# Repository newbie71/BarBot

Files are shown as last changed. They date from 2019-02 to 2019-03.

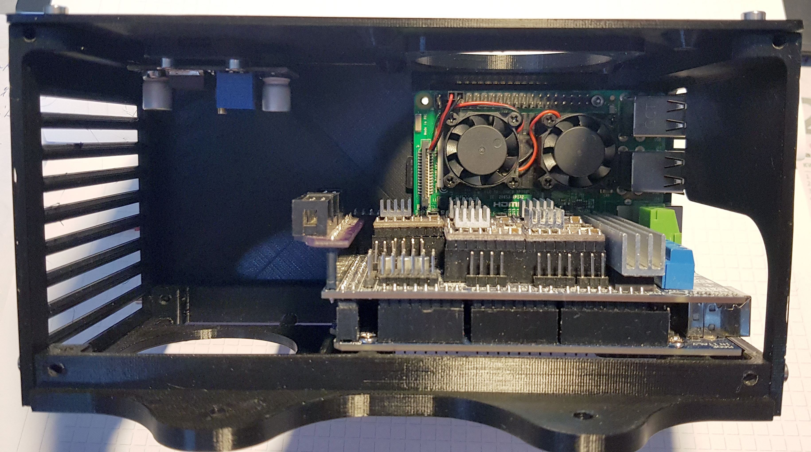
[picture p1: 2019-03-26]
Pics/20190226_145837a.jpg

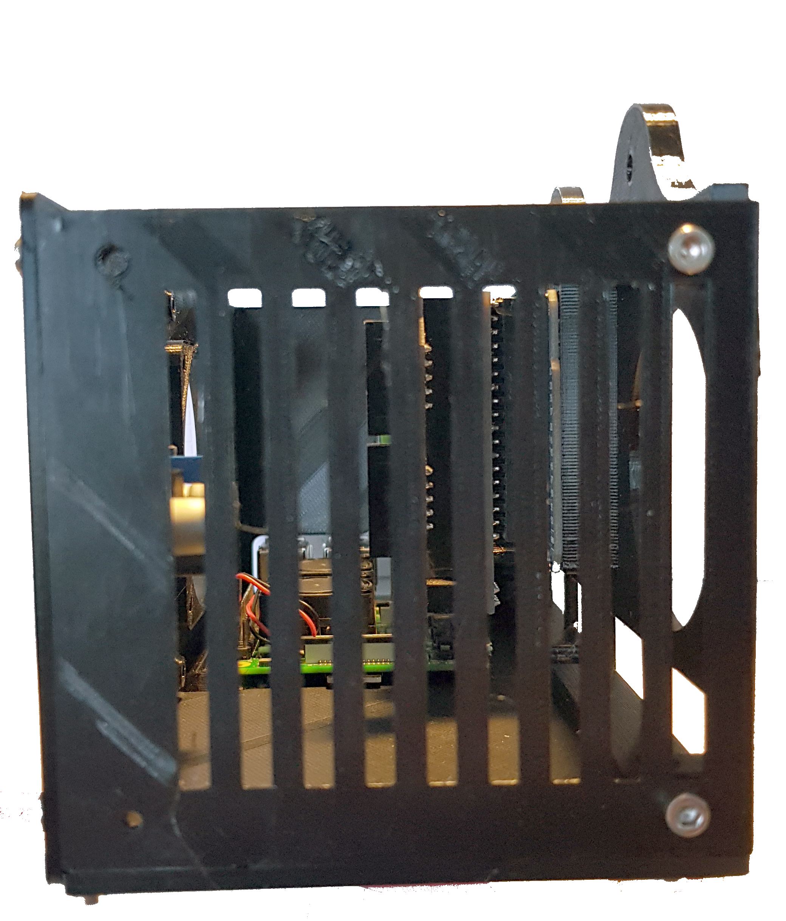
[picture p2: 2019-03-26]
Pics/20190226_150021a.jpg

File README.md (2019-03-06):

# BarBot fork from sexycyborg
An Automated Bartender powered by Arduino  

Based on the work of Lukas Šidlauskas:  
https://create.arduino.cc/projecthub/sidlauskas/barbot-cocktail-mixing-robot-0318aa  
https://github.com/sidlauskaslukas/barbot

Based on the work of Naomi Wu

https://github.com/sexycyborg/BarBot/

## About

For my BarBot I wanted to make sure it was rock-solid reliable.
16 popular drinks (15 alcoholic and 1 non-alcoholic for non-drinkers and so that children can participate with supervision) are available from 16 arcade style buttons. A printed menu lists what button number corresponds to which drink.

Since the BarBot is designed for a working bars, party or company environments, it had to do without pumps or difficult to clean feed lines. All of the components that require nightly cleaning are the same that bar staff are already accustomed to cleaning- spirit measures and bar mats. All drive components and bearings have been moved from under the pour spouts to well above or behind so there is no risk of an accumulation of sugar-rich liquids gumming up hard to clean moving parts of the machine or attracting vermin.

This BarBot is a functional novelty- it's something fun for visitors to play with. Perfect for my home and company where a large number of patrons are tech professionals. It is not secured for true commercial use- and with a bar full of half-drunk hardware engineers it would be pointless to try. In this case, it's better to rely on good faith then pretend you could stop them if challenged. Patrons could still manually press their cups to the spirit measures to manually dispense alcohol if they wanted to- but they could also reach over the bar and steal liquor while the bartender's back was turned. So far none have because why ruin the fun when there's no "hack" in doing so? If you really wanted to, a clear acrylic panel could be added to the front to prevent any manual dispensing, but it's really a lot less fun that way.

Portion control and payment is handled via an inexpensive arcade token acceptor. A customer can pay the bartender for a cup of ice and a token. When the correct token is inserted into the BarBot a contact is momentarily closed. The customer then has 60 seconds to press a drink selection button. That same contact can be closed with the key switch, in which case no tokens are needed for any orders while the switch is in that position.

Barbots of this configuration typically use either a servo or a stepper motor with a lead screw to depress the spirit measure spout depending on the type of dispenser it is. My code changes allow for either as RAMPS boards can control both steppers and a servo.

In the build and demonstration videos, you'll see that the full 25ml "shot" the spirit measure contains is usually only partially dispensed. This is because the actual shot size is defined in the code as a function of how long the spout is depressed. This allows for finer tuning of the drink flavor and portion size which would not be possible if only 25ml increments were used.

This BarBot was designed to be easy to build with off-the-shelf OpenBuilds components, V-Slot aluminum extrusion, and low-cost 3D printer parts. The heart of the BarBot is a standard Arduino Mega, RAMPS 1.6 and TMC2xxx or DRV8825 stepper driver combination as used in many 3D printers. But my prefered combination is a BIQU re-arm clone,RAMPS 1.6+ and TMC2130 V1.1 spi.

BarBot<BR>
See [Build Guide](https://github.com/sexycyborg/BarBot/blob/master/BarBotDrwMk01.PDF). 
  *Guide and SolidWorks CAD drawings courtesy of [Vexelius](https://www.thingiverse.com/Vexelius/).*

## Attention this BOM variats from the Sexyborg due to high cost's and shipment from openbuilds-store  
### All sources including prices can be found in the BOM Excel-sheet

## BOM

The BOM can be found here https://github.com/newbie71/BarBot/blob/master/BOM_Barbot_1.0.xlsx 
with links where to order and the cost.

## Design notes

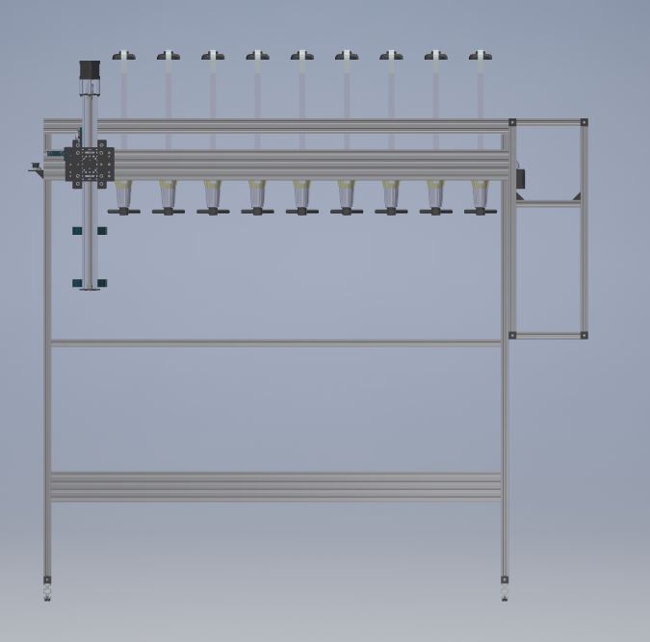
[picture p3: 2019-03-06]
Pics/Barbot_04.JPG

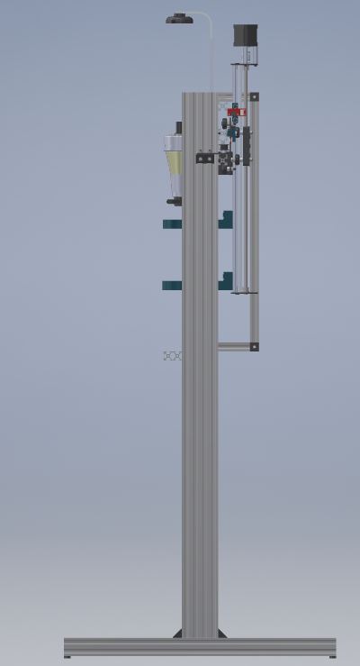
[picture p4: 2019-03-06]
Pics/Barbot_02.JPG

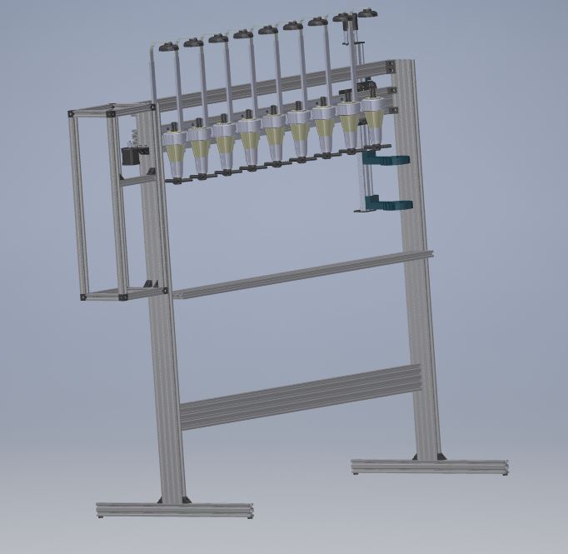
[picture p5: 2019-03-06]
Pics/Barbot_05.JPG

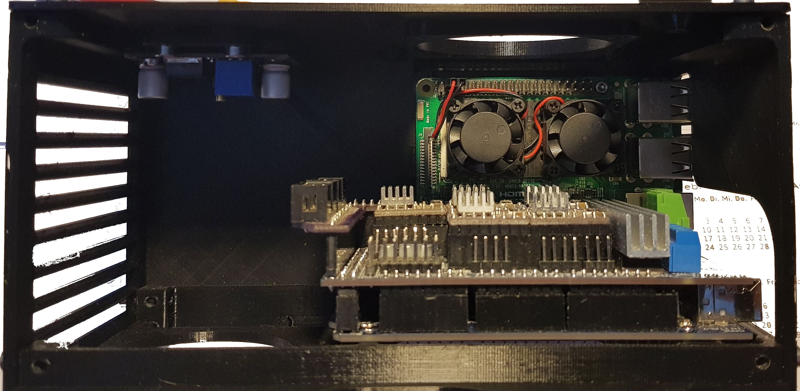
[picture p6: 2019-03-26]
Pics/20190226_145816_a.jpg

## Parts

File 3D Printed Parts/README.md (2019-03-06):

# Naomi Wu's BarBot
An Automated Bartender powered by Arduino  

All parts can be printed in PETG at 0.2mm layer height, 30% infill.

## Additional 3D Files Required:

[Quick Release RAMPS Holder for T-Slot Profile](https://www.thingiverse.com/thing:2169986)  

[2020 Cable Zip Tie Mount for M5x10 screws (optional fins)](https://www.thingiverse.com/thing:2486032)

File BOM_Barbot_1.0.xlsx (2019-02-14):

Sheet: newbie71
QTY | Description | Source
 |  |  | SP | TP
Frame |  |  | EP2 | GP2
1.00 | Ramps Kit 1.4 | Ramps 1.4 kit (https://www.aliexpress.com/item/3D-Printer-1pc-Mega-2560-R3-1pc-RAMPS-1-4-control-panel-5pcs-DRV8825-Stepper-Motor/32599773680.html) | 16.66 | 16.66 | €
1.00 | Ramps SD Card Reader | SD Card-Ramps (https://www.aliexpress.com/item/New-TF-SD-Card-SD-Ramps-3D-Printer-Assembling-Module-For-Ramps-1-4-Diy-Kit/32958286211.html) | 1.09 | 1.09 | €
2.00 | 10x10 Drag chain 2 Meters | Drag-Chain-L1000mm (https://www.aliexpress.com/item/Drag-Chain-L1000mm-Transmission-Chains-10-x-10mm-Cable-Wire-Carrier-with-end-connectors-for-CNC/32852286371.html) | 4.16 | 8.32 | €
1.00 | V-Slot 1200mm (horizontal carriage rail) | v-slot linear Rail 1200mm (https://jamoprint.com/CNC-Profile-Linearprofile---Zubehoer/Alu-Profile/CNC-Linearprofil-V-Slot-20x20x1000-28-29-30-48.html) | 30.90 | 30.90 | €
2.00 | Alu-Profile 2080 1200mm (Two vertical risers ) | Alu-Profile 2080 (https://www.ebay.de/i/323427289717?chn=ps&var=512489777539) | 25.00 | 50.00 | €
2.00 | Alu-Profile 2080 1160mm (Lower brace, shelf for bar mat) | Alu-Profile 2080 (https://www.ebay.de/i/323427289717?chn=ps&var=512489777539) | 25.00 | 50.00 | €
1.00 | Alu-Profile 2040, 1200mm (Horizontal rail for drag chain) | Alu-Profile 2040 (https://www.ebay.de/itm/Systemprofil-20x40-2040-Nut-6-Strebenprofil-Aluprofil-Konstruktionsprofil/323655543211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) | 17.10 | 17.10 | €
2.00 | Alu-Profile 2040 600mm (Horizontal legs) | Alu-Profile 2040 (https://www.ebay.de/itm/Systemprofil-20x40-2040-Nut-6-Strebenprofil-Aluprofil-Konstruktionsprofil/323655543211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) | 8.70 | 17.40 | €
1.00 | V-Slot® NEMA 17 Linear Actuator Bundle 500mm | V-Slot sliding table 500mm (https://www.aliexpress.com/item/Effective-travel-400mm-linear-Sliding-table-total-length-494mm-T8-Screw-2060-V-slot-with-42/32917601483.html) | 47.82 | 47.82 | €
1.00 | V-Slot Gantry Set , 20mm - 80mm (Universal) | V-Slot-Gantry-Set (https://www.aliexpress.com/item/Funssor-Assembled-Black-Color-V-Slot-Gantry-Set-For-DIY-Openbuilds-CNC-milling/32957873797.html) | 14.39 | 14.39 | €
1.00 | Motor Mount Plate Nema17 | V-Slot-NEMA-17-Linear-Actuator-Bundle-Kit (https://www.aliexpress.com/item/V-Slot-NEMA-17-Linear-Actuator-Bundle-Diy-Belt-Driven-Kit-with-Nema-17-Stepper-Motor/32899784879.html) | 35.61 | 35.61 | €
2.00 | GT2-2m Timing Belt (per Meter) | GT2-2M 6MM (https://www.aliexpress.com/item/2M-3D-Printer-Accessories-2GT-6MM-10MM-PU-with-steel-core-GT2-Open-Timing-Belt-Width/32857079977.html) | 2.06 | 4.12 | €
2.00 | Black Angle Corner Connector | 25pcs-Cast-Corner-Bracket-for-V-Slot-T-slot (https://www.aliexpress.com/item/25pcs-lot-CNC-Aluminum-90-Degree-Cast-Corner-Bracket-for-V-Slot-T-slot-Linear-Rail/32870718238.html) | 9.99 | 19.98 | €
3.00 | M5*8 Low Profile Screws (10 pcs/pack) | 20pcs-M5-Low-Profile-Screws-M5 (https://www.aliexpress.com/item/3D-printer-parts-20pcs-M5-Low-Profile-Screws-M5-6-8-10-12-15-20-25mm/32963232719.html) | 0.97 | 2.91 | €
1.00 | M5*40 Low Profile Screws (10 pcs/pack) | Zylinderschrauben-DIN-7984-Edelstahl-V2A-M5-niedrig (https://www.ebay.de/itm/Zylinderschrauben-DIN-7984-Edelstahl-V2A-M5-niedrig-Innensechskant/281264548516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) | 2.30 | 2.30 | €
1.00 | M5*25 Low Profile Screws (10 pcs/pack) | 20pcs-M5-Low-Profile-Screws-M5x25mm (https://www.aliexpress.com/item/3D-printer-parts-20pcs-M5-Low-Profile-Screws-M5-6-8-10-12-15-20-25mm/32963232719.html) | 2.02 | 2.02 | €
1.00 | 3mm Aluminium Spacer | 3mm Aluminium Spacer (https://www.ebay.de/itm/Distanz-H%C3%BClse-M5-Abstandshalter-Distanzh%C3%BClse-Huelse-H%C3%BClse-Aluminium-dely-trade/121237081001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) | 2.41 | 2.41 | €
1.00 | 6mm Aluminium Spacer | 6mm Aluminium Spacer (https://www.aliexpress.com/item/5pcs-Bicycle-Water-Bottle-Holder-Spacer-M5-Washer-Aluminum-Alloy-6mm-Bike-Parts/32911691819.html) | 0.81 | 0.81 | €
1.00 | Tee Nuts M5 (10 pcs/pack) | 50pcs V-Slot-M5-Tee-Nut (https://www.aliexpress.com/item/50pcs-Lot-Micromake-3D-Printer-Parts-Tee-nuts-for-building-machine-V-Slot-M5-Tee-Nut/32689972745.html) | 4.87 | 4.87 | €
1.00 | Drop in Tee Nuts M5 | M5-Nickel-Plated-Tee-Nut-Hammer-Head-Attach-Nut (https://www.aliexpress.com/item/M3-M4-M5-Nickel-Plated-Tee-Nut-Hammer-Head-Attach-Nut-for-Aluminum-Extrusion-Profile-2020/32964717506.html) | 4.95 | 4.95 | €
1.00 | Nylon Insert Hex Locknut M5 (10 pcs/pack) | 50pcs-DIN98 M5 (https://www.aliexpress.com/item/50Pcs-DIN985-M2-M2-5-M3-M4-M5-M6-or-M8-20pcs-304-Stainless-Steel-Nylon/32865488252.html) | 3.59 | 3.59 | €
2.00 | 1250mm Slot Cover /Panel Holder | 1m 20-30-40-50-series-6mm-8mm-10mm-flat-seal (https://www.aliexpress.com/item/1meter-20-30-40-50-series-6mm-8mm-10mm-flat-seal-for-2020-aluminum-profile-soft/32840481329.html) | 0.76 | 1.52 | €
2.00 | Bar Mat | Barkeeper-Service-Matte-Trockenschalen (https://www.amazon.de/COSOOS-Gummi-%C3%9Cberlaufmatte-versch%C3%BCttungsfreies-Kaffee-Barkeeper-Service-Matte-Trockenschalen-Matten/dp/B07L46CCF3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) | 8.99 | 17.98 | €
Control Box
4.00 | Alu-Profile 2020 530mm (All with 5mm threaded ends) | Alu-Profile 2020 Nut-5 (https://www.ebay.de/itm/Aluminiumprofil-20x20-Nut-5-Alu-Profil-5-Strebenprofil-item-2020-100mm-1200mm/112881130983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) | 5.50 | 22.00 | €
5.00 | Alu-Profile 2020 165mm (All with 5mm threaded ends) | Alu-Profile 2020 Nut-5 (https://www.ebay.de/itm/Aluminiumprofil-20x20-Nut-5-Alu-Profil-5-Strebenprofil-item-2020-100mm-1200mm/112881130983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) | 1.50 | 7.50 | €
4.00 | Alu-Profile 2020 130mm (All with 5mm threaded ends) | Alu-Profile 2020 Nut-5 (https://www.ebay.de/itm/Aluminiumprofil-20x20-Nut-5-Alu-Profil-5-Strebenprofil-item-2020-100mm-1200mm/112881130983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) | 2.00 | 8.00 | €
8.00 | Cube Corner | V-slot-three-corner-cube-corner (https://www.aliexpress.com/item/3D-printer-openbuilds-V-slot-three-corner-cube-corner-prism-connector-adjustable-wheel-bracket-1pcs/32790791649.html) | 1.00 | 8.00 | €
2.00 | M5*15 Low Profile Screws (10 pcs/pack) | 20pcs-M5-Low-Profile-Screws-M5 (https://www.aliexpress.com/item/3D-printer-parts-20pcs-M5-Low-Profile-Screws-M5-6-8-10-12-15-20-25mm/32963232719.html) | 1.45 | 2.90 | €
1.00 | Coin Acceptor (Or similar if you modify the lower lasercut panel to fit) | Multi-Coin-Acceptor-CPU-Programmable (https://www.aliexpress.com/item/Multi-Coin-Acceptor-CPU-Programmable-6-Type-Coin-Validator-Electronic-Selector-Mechanism-Arcade-Mech-for-Vending/32901295765.h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) | 10.99 | 10.99 | €
2.00 | 27x27 Illuminated Arcade Buttons (min lot 20 pcs) | 27x27mm-Small-square-LED-Light-Illuminated-push-button (https://www.aliexpress.com/item/27-27mm-Small-square-LED-Light-Illuminated-push-button-switch-for-casino-slot-machine-gambling-game/32860066542.html) | 12.78 | 25.56 | €
1.00 | 22mm Emergency Stop Push Button Switch 12V DC LED Illuminated (or similar) | LAY7-Y090 Emergency-stop-light-power-22mm-switches (https://www.aliexpress.com/item/Emergency-stop-light-power-22mm-switches-mushroom-head-on-off-pushbutton-led-switch-lay37-lay7-Y090/32962801033.html) | 3.62 | 3.62 | €
1.00 | 22mm Key Selector Switch | LAY37-AC-380V-10A-DPST-3-Position-Rotary-Selector-Key-Lock-Switch (https://www.aliexpress.com/item/LAY37-AC-380V-10A-DPST-3-Position-Rotary-Selector-Key-Lock-Switch-1-N-O-1/32864589832.html) | 1.58 | 1.58 | €
1.00 | Power Socket Switch IEC 320 C14 | Panel-Mount-Rocker-Switch-IEC320-C14-3-Pin-Plug (https://www.ebay.de/itm/Panel-Mount-Rocker-Switch-IEC320-C14-3-Pin-Plug-Power-Socket-AC250V-10A-ST/192790286152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) | 1.55 | 1.55 | €
1.00 | 12v Power Supply, 150w (Part No. MS-150-12 or similar) | DC-12V-LED Power Supply (https://www.ebay.de/itm/DC-12V-24V-2A-30A-LED-Netzteil-Trafo-Schaltnetzteil-Adapter-Treiber-Power-Supply/162296585279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) | 19.67 | 19.67 | €
1.00 | Ribbon cable to 18 pin connector 40CM long | 1m-Flat-IDC-Ribbon-Extension-Cable (https://www.aliexpress.com/item/1m-Flat-IDC-Ribbon-Extension-Cable-Rainbow-DuPont-Wire-10P-14P-16P-20P-26P-34P-40P/32964398452.html) | 1.07 | 1.07 | €
 |  |  |  | 469.19 | €

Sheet: Sexycyborg BOM
QTY | Description | Source
 |  |  | SP | TP
1.00 | Ramps Kit 1.4 | Available as a kit (https://www.gearbest.com/kits/pp_228312.html?lkid=11066669) | 36.41 | 36.41 | $
1.00 | Ramps SD Card Reader | 1x RAMPS 1.4/1.5 SD Card Reader (http://amzn.to/2EYiyeb) | 4.49 | 4.49 | $
1.00 | 10x10 Drag chain 2 Meters | 10x10 Drag Chain (http://amzn.to/2ECHM3W) | 17.22 | 17.22 | $
1.00 | V-Slot 1200mm (horizontal carriage rail) | V-Slot® 20x80 Linear Rail (http://openbuildspartstore.com/v-slot-20x80-linear-rail/) | 28.27 | 28.27 | €
2.00 | Alu-Profile 2080 1200mm (Two vertical risers ) | V-Slot® 20x80 Linear Rail (http://openbuildspartstore.com/v-slot-20x80-linear-rail/) | 28.27 | 56.54 | €
2.00 | Alu-Profile 2080 1160mm (Lower brace, shelf for bar mat) | V-Slot® 20x80 Linear Rail | 28.27 | 56.54 | €
1.00 | Alu-Profile 2040, 1200mm (Horizontal rail for drag chain) | V-Slot® 20x40 Linear Rail (http://openbuildspartstore.com/v-slot-20x40-linear-rail/) | 18.55 | 18.55 | €
2.00 | Alu-Profile 2040 600mm (Horizontal legs) | V-Slot® 20x40 Linear Rail (http://openbuildspartstore.com/v-slot-20x40-linear-rail/) | 12.36 | 24.72 | €
1.00 | V-Slot® NEMA 17 Linear Actuator Bundle 500mm | V-Slot® NEMA 17 Linear Actuator Bundle (http://openbuildspartstore.com/v-slot-nema-17-linear-actuator-bundle-lead-screw/) | 127.24 | 127.24 | €
1.00 | V-Slot Gantry Set , 20mm - 80mm (Universal) | V-Slot Gantry Set (http://openbuildspartstore.com/v-slot-gantry-set/) | 28.27 | 28.27 | €
1.00 | Motor Mount Plate Nema17 | Motor Mount Plate - NEMA 17 (http://openbuildspartstore.com/motor-mount-plate-nema-17-stepper-motor/) | 6.18 | 6.18 | €
1.00 | Idler Pulley Plate | Idler Pulley Plate (http://openbuildspartstore.com/idler-pulley-plate/) | 6.18 | 6.18 | €
1.00 | Smooth Idler Pulley Kit | Smooth Idler Pulley Kit (http://openbuildspartstore.com/smooth-idler-pulley-kit/) | 5.29 | 5.29 | €
3.00 | GT2-2m Timing Belt (per Meter) | GT2-2M Timing Belt (http://openbuildspartstore.com/gt2-2m-timing-belt/) | 2.20 | 6.6 | €
1.00 | GT2-2m Timing Pulley 20 Tooth | GT2-2M Timing Pulley - 20 Tooth (http://openbuildspartstore.com/gt2-2m-timing-pulley-20-tooth/) | 5.29 | 5.29 | €
1.00 | Nema 17 Stepper Motor | NEMA 17 Stepper Motor (http://openbuildspartstore.com/nema-17-stepper-motor/) | 15.90 | 15.9 | €
30.00 | Black Angle Corner Connector | Black Angle Corner Connector (http://openbuildspartstore.com/black-angle-corner-connector/) | 2.64 | 79.2 | €
6.00 | M5*8 Low Profile Screws (10 pcs/pack) | Openbuilds Low Profile Screws (http://openbuildspartstore.com/low-profile-screws-m5/) | 1.23 | 7.38 | €
1.00 | M5*40 Low Profile Screws (10 pcs/pack) | Openbuilds Low Profile Screws (http://openbuildspartstore.com/low-profile-screws-m5/) | 1.85 | 1.85 | €
1.00 | M5*25 Low Profile Screws (10 pcs/pack) | Openbuilds Low Profile Screws | 1.58 | 1.58 | €
1.00 | M5*15 Low Profile Screws (10 pcs/pack) | Openbuilds Low Profile Screws | 1.41 | 1.41 | €
1.00 | 3mm Aluminium Spacer | Aluminum Spacer (http://openbuildspartstore.com/aluminum-spacers/) | 2.20 | 2.2 | €
1.00 | 6mm Aluminium Spacer | Aluminum Spacer (http://openbuildspartstore.com/aluminum-spacers/) | 2.64 | 2.64 | €
5.00 | Tee Nuts M5 (10 pcs/pack) | Tee Nuts (http://openbuildspartstore.com/tee-nuts-25-pack/) | 2.64 | 13.2 | €
50.00 | Drop in Tee Nuts M5 | Drop In Tee Nuts (http://openbuildspartstore.com/drop-in-tee-nuts/) | 0.87 | 43.5 | €
3.00 | Nylon Insert Hex Locknut M5 (10 pcs/pack) | Nylon Insert Hex Locknut - M5 (http://openbuildspartstore.com/nylon-insert-hex-locknut-m5/) | 0.87 | 2.61 | €
1 | 1250mm Slot Cover /Panel Holder | Slot Cover™ / Panel Holder (http://openbuildspartstore.com/slot-cover-panel-holder/) | 4.53 | 4.53 | €
2 | Bar Mat | Bar mat (http://amzn.to/2Eo2QvR) | 8.99 | 17.98
Control Box
4 | Alu-Profile 2020 530mm (All with 5mm threaded ends) | V-Slot® 20x20 Linear Rail (http://openbuildspartstore.com/v-slot-20x20-linear-rail/) | 9.45 | 37.8 | €
5 | Alu-Profile 2020 165mm (All with 5mm threaded ends) | V-Slot® 20x20 Linear Rail (http://openbuildspartstore.com/v-slot-20x20-linear-rail/) | 2.91 | 14.55 | €
4 | Alu-Profile 2020 130mm (All with 5mm threaded ends) | V-Slot® 20x20 Linear Rail (http://openbuildspartstore.com/v-slot-20x20-linear-rail/) | 2.91 | 11.64 | €
8 | Cube Corner | Cube Corner Connector (http://openbuildspartstore.com/cube-corner-connector/) | 3.08 | 24.64 | €
3 | M5*15 Low Profile Screws (10 pcs/pack) | Openbuilds Low Profile Screws (http://openbuildspartstore.com/low-profile-screws-m5/) | 1.41 | 4.23 | €
1 | Coin Acceptor (Or similar if you modify the lower lasercut panel to fit) | Coin Acceptor (https://item.taobao.com/item.htm?id=540305747207) | 23.56 | 23.56 | $
20 | 27x27 Illuminated Arcade Buttons (min lot 20 pcs) | 27x27 Illuminated Arcade Buttons (https://www.aliexpress.com/store/product/27-27mm-quadrate-LED-Light-Illuminated-Full-Colors-Push-Button-With-Micro-Switch-Master-Arcade-DIY/1960309_3255916440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) | 1.52 | 30.4 | $
1 | 22mm Emergency Stop Push Button Switch 12V DC LED Illuminated (or similar) | 22mm Emergency Stop Push Button Switch (http://amzn.to/2Chvvgb) | 14.95 | 14.95 | $
1 | 22mm Key Selector Switch | 22mm Key Selector Switch (http://amzn.to/2ErJs0M) | 14.95 | 14.95 | $
1 | Power Socket Switch IEC 320 C14 | Power Socket Switch IEC 320 C14 (http://amzn.to/2HcuYjs) | 9.99 | 9.99 | $
1 | 12v Power Supply, 150w (Part No. MS-150-12 or similar) | 12v Power Supply, 150w (https://www.aliexpress.com/item/MS-150-12-mini-size-12-5a-led-psu-150w-12v-power-supply/32663431069.html) | 23.57 | 23.57 | $
1 | Ribbon cable to 18 pin connector 40CM long | Ribbon cable to 18 pin connector 40CM long (https://item.taobao.com/item.htm?id=520267411024) | 0.42 | 0.42 | $
 |  |  |  | 832.47

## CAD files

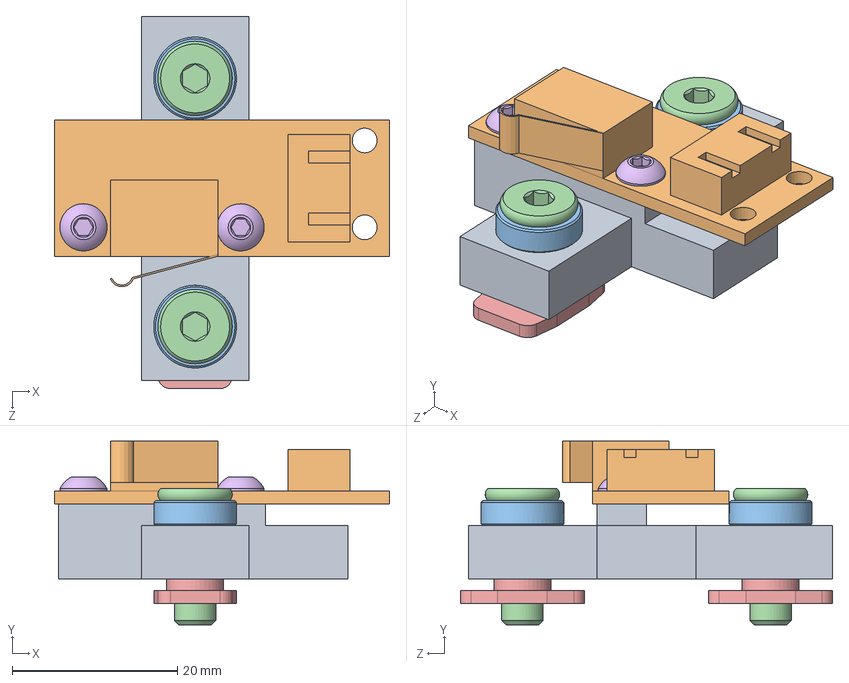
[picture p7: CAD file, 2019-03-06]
CAD Files/SolidWorks/Z-Axis Endstop.SLDASM
40.5 x 22.2 x 45.0 mm
ZAxis Endstop Holder
RAMPSEndStop
Aluminum Spacer 3mm x 2
Low Profile Screw M5 x 2
Tee Nut x 2
Button Head Socket Cap Screw M3 x 2

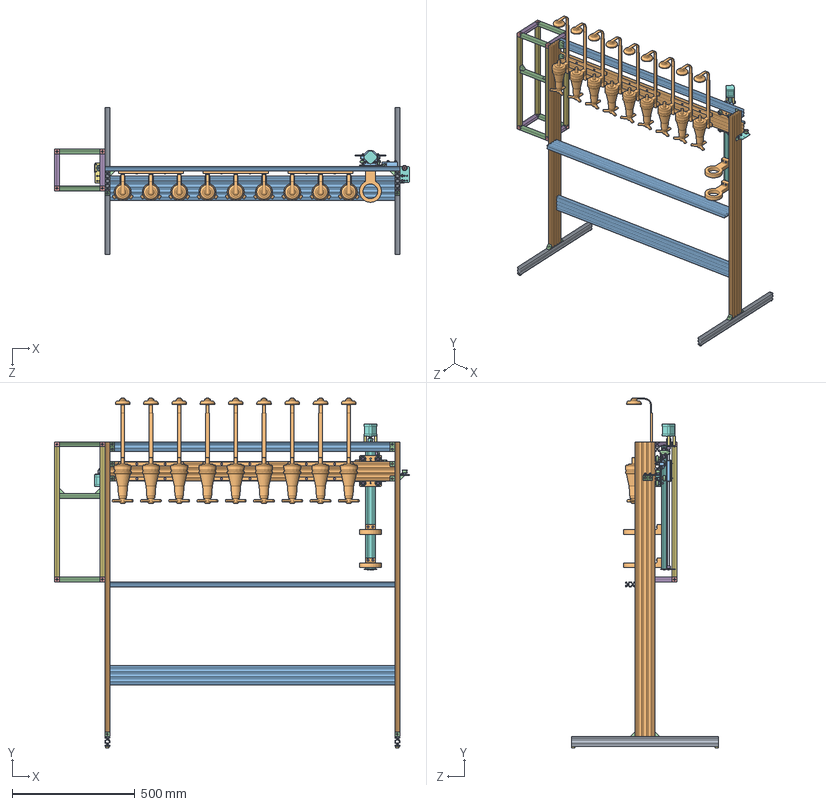
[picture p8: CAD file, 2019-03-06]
CAD Files/SolidWorks/BarBot.SLDASM
1444.5 x 1423.2 x 600.0 mm
V-Slot 20x40x600 x 2
V-Slot 20x80x1200 x 3
V-Slot 20x40x1200
Black Angle Corner Connector x 20
Tee Nut x 12
Low Profile Screw M5 x 42
RubberPad x 4
Idler Pulley Plate
STDNut x 12
STDWasher x 12
Aluminum Spacer 6mm x 7
Smooth Idler Pulley Wheel
Ball Bearing 5 x 16 x 5 x 18
Nylon Spacer 0.125in
Motor Mount Plate Nema 17
Nema 17 Stepper Motor x 2
GT2 Timing Pulley 20 Tooth
Bar Butler x 3
V-Slot 20x80x1160 x 2
V-Slot 20x20x165 x 5
Cube Corner Connector x 8
V-Slot 20x20x130 x 4
V-Slot 20x20x530 x 4
Self Tapping Screw x 4
Socket Head Cap Screw M3 x 3
Nylon Insert Lock Nut M5 x 6
Threaded Rod Plate Nema 17 x 2
Ball Bearing 8 x 16 x 5 x 2
Shim Washer 8mm x 2
Lock Collar 8mm x 2
Aluminum Spacer 1.5in x 3
Flexible Coupling 5mm x 8mm
8mm leadscrew 520mm
V-Slot Gantry Plate 20-80mm x 2
Spacer Block x 2
Solid V Wheel x 8
Precision Shim 10 x 5 x 1 x 8
8mm Acme Nut Block
Eccentric Spacer 6mm x 2
V-Slot 20x40x500 Linear Rail
Aluminum Spacer 3mm x 8
CupRing x 2
XAxis Endstop Holder
RAMPSEndStop x 2
Button Head Socket Cap Screw M3 x 4
ZAxis Endstop Holder

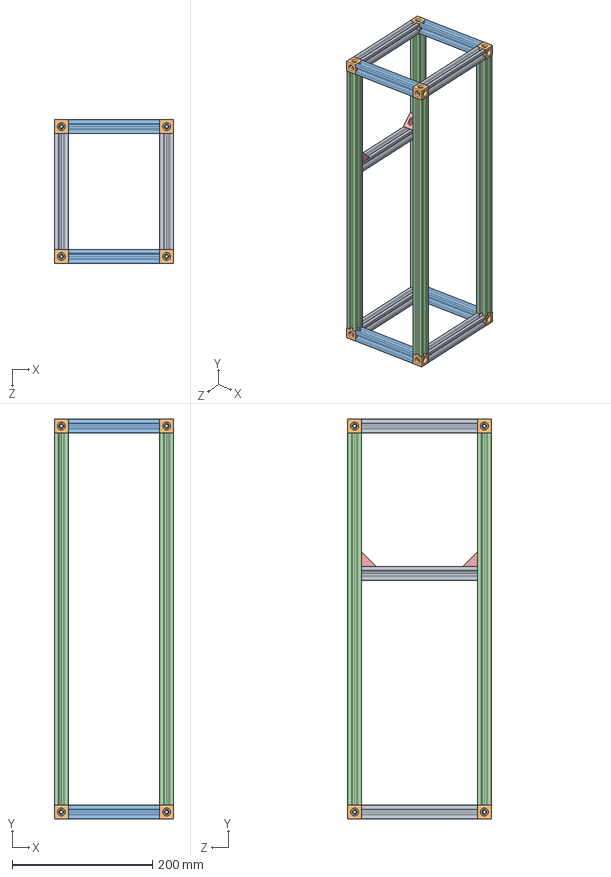
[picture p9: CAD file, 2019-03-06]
CAD Files/SolidWorks/Control Box.SLDASM
170.0 x 570.0 x 205.0 mm
V-Slot 20x20x165 x 5
Cube Corner Connector x 8
V-Slot 20x20x130 x 4
V-Slot 20x20x530 x 4
Black Angle Corner Connector x 2

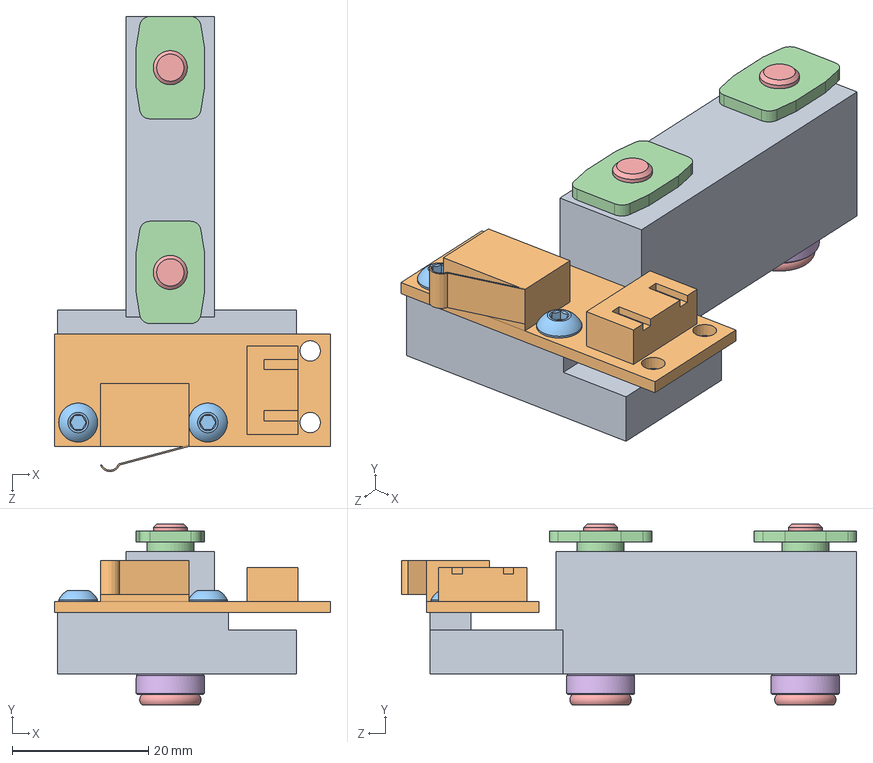
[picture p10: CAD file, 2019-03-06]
CAD Files/SolidWorks/X-Axis Endstop.SLDASM
40.5 x 26.5 x 66.7 mm
XAxis Endstop Holder
RAMPSEndStop
Button Head Socket Cap Screw M3 x 2
Tee Nut x 2
Low Profile Screw M5 x 2
Aluminum Spacer 3mm x 2

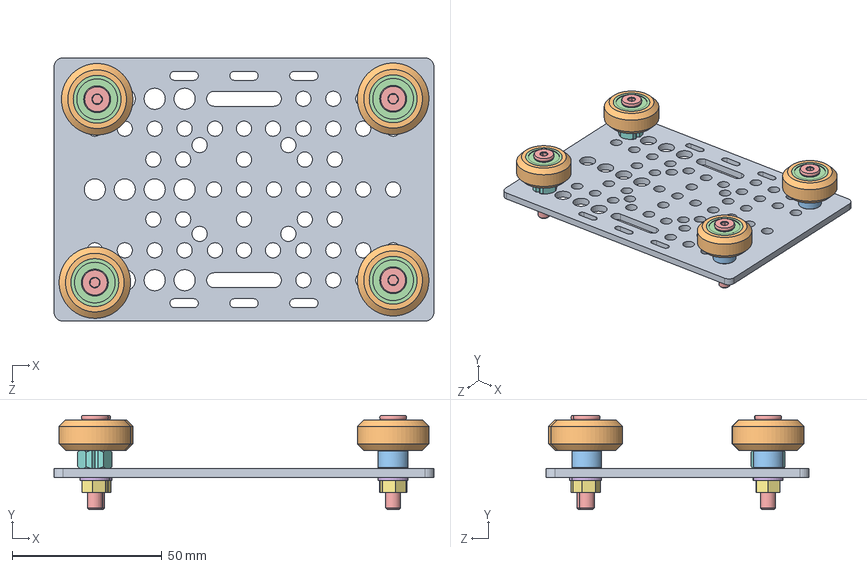
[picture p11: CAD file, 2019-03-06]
CAD Files/SolidWorks/Dispenser Carriage.SLDASM
127.0 x 31.5 x 88.0 mm
V-Slot Gantry Plate 20-80mm
Solid V Wheel x 4
Aluminum Spacer 6mm x 2
Ball Bearing 5 x 16 x 5 x 8
Low Profile Screw M5 x 4
STDWasher x 4
STDNut x 4
Eccentric Spacer 6mm x 2

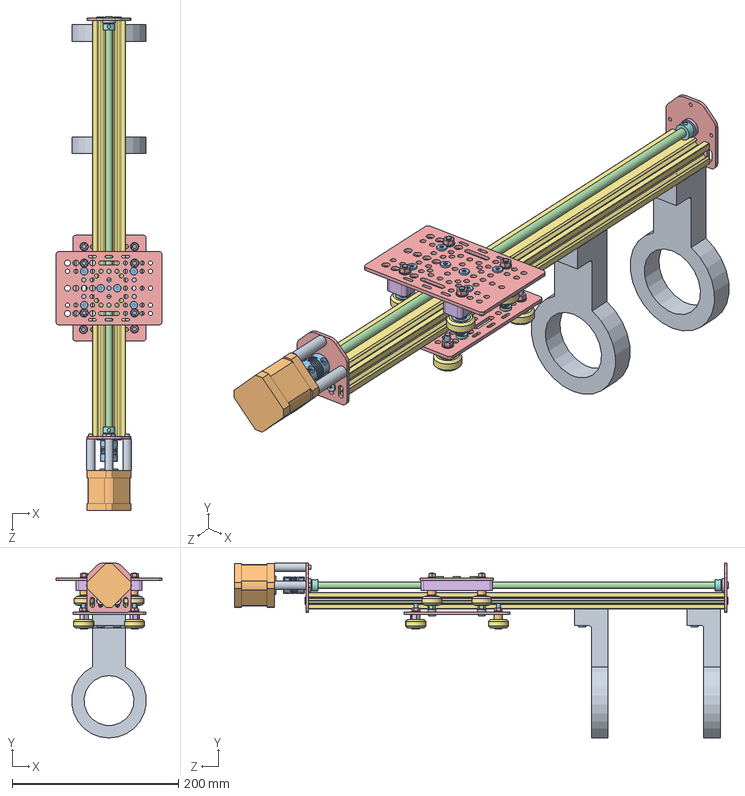
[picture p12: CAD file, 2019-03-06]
CAD Files/SolidWorks/Dispenser Actuator.SLDASM
127.0 x 210.3 x 594.1 mm
Self Tapping Screw x 4
Socket Head Cap Screw M3 x 3
Low Profile Screw M5 x 18
Nylon Insert Lock Nut M5 x 6
Threaded Rod Plate Nema 17 x 2
Ball Bearing 8 x 16 x 5 x 2
Shim Washer 8mm x 2
Lock Collar 8mm x 2
Aluminum Spacer 1.5in x 3
Nema 17 Stepper Motor
Flexible Coupling 5mm x 8mm
8mm leadscrew 520mm
V-Slot Gantry Plate 20-80mm x 2
Spacer Block x 2
Solid V Wheel x 8
Ball Bearing 5 x 16 x 5 x 16
Precision Shim 10 x 5 x 1 x 8
Aluminum Spacer 6mm x 6
8mm Acme Nut Block
STDWasher x 8
STDNut x 8
Eccentric Spacer 6mm x 2
V-Slot 20x40x500 Linear Rail
Aluminum Spacer 3mm x 4
CupRing x 2
Tee Nut x 4

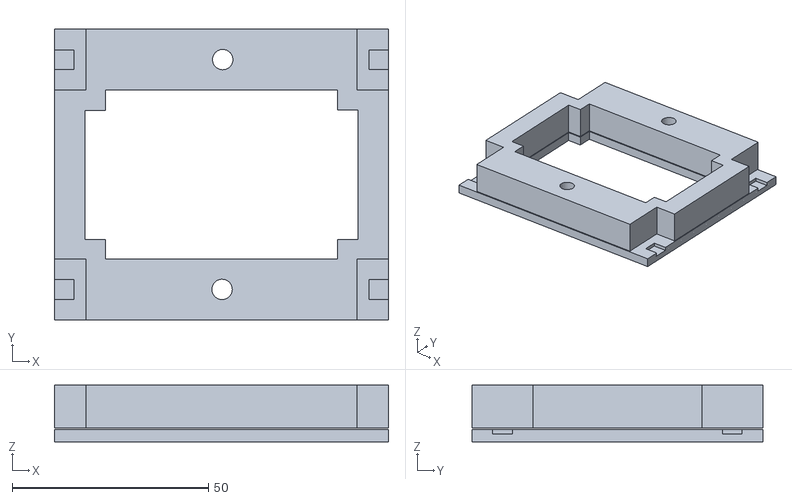
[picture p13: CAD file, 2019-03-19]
3D Printed Parts/cbb.stl
85.0 x 74.0 x 14.5

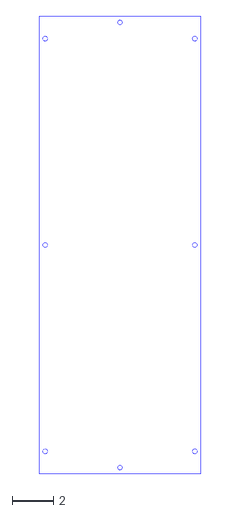
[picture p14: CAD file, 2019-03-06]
CAD Files/Laser Cut Panels/565mm x 200mm- Back v1.dxf
7.88 x 22.2

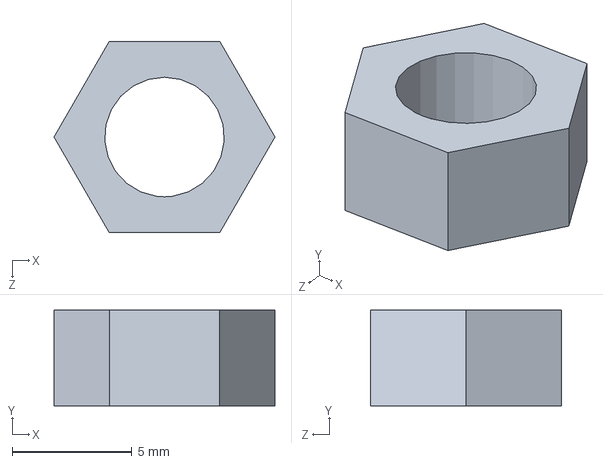
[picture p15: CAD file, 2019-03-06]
CAD Files/SolidWorks/STDNut.SLDPRT
9.24 x 4.00 x 8.00 mm

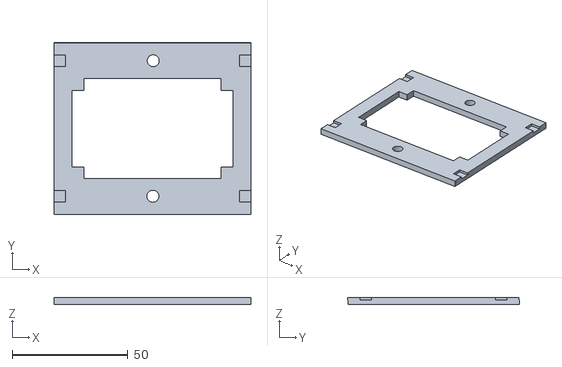
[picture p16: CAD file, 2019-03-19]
3D Printed Parts/cbb1.stl
85.0 x 74.0 x 3.20

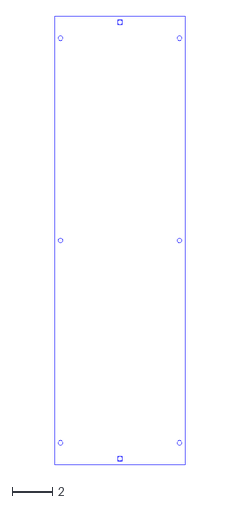
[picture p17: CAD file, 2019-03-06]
CAD Files/Laser Cut Panels/565mm x 165mm- Side v1.dxf
6.50 x 22.2

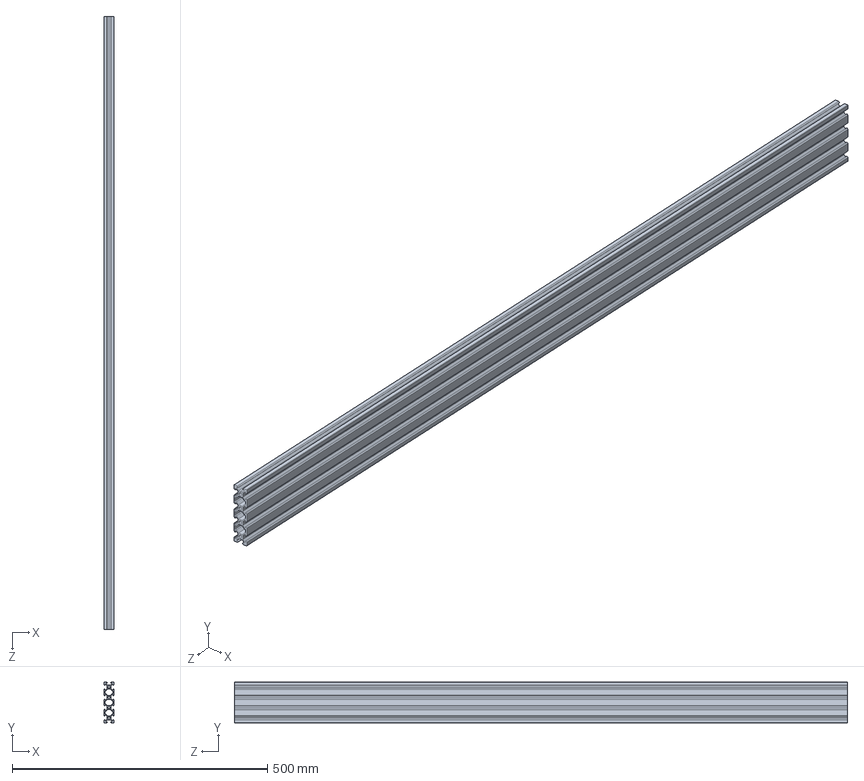
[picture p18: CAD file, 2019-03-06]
CAD Files/SolidWorks/V-Slot 20x80x1200.SLDPRT
20.0 x 80.0 x 1200.0 mm

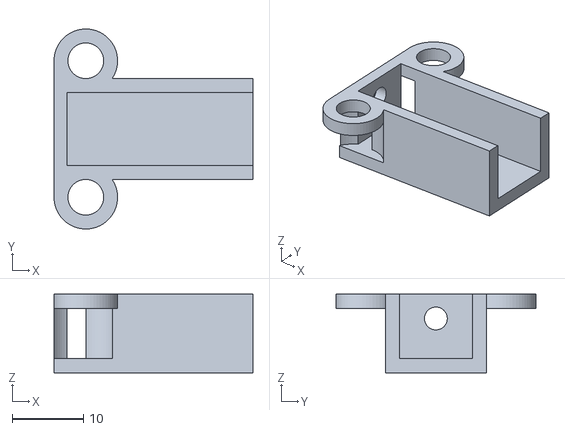
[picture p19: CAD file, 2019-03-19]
3D Printed Parts/Belt-tensioner.stl
27.9 x 28.0 x 11.0

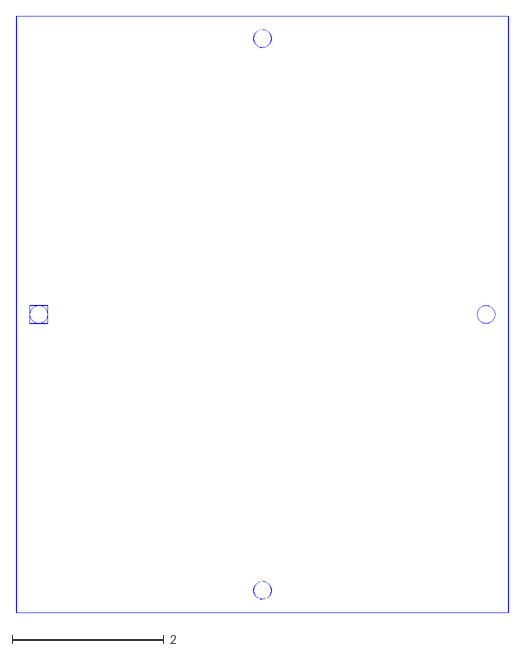
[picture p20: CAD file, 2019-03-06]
CAD Files/Laser Cut Panels/200mm x 165mm- Bottom v1.dxf
6.50 x 7.88

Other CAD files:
CAD Files/SolidWorks/ZAxis Endstop Holder.SLDPRT
3D Printed Parts/v-slot_idler_plate.stl
3D Printed Parts/v-slot_stepper_plate.stl
3D Printed Parts/Display_back.stl
3D Printed Parts/Display_front.stl
3D Printed Parts/Level-Shifter.stl
3D Printed Parts/Ramps_Box_1.4_Base_V2_2020_RPI3.stl
3D Printed Parts/Ramps_Box_1.4_Bottom_2020.stl
3D Printed Parts/Ramps_Box_1.4_Fan.stl
3D Printed Parts/Ramps_Box_1.4_Left_Grid.stl
3D Printed Parts/Ramps_Box_1.4_PT100-60mm-Fan_Front-V2.stl
3D Printed Parts/Ramps_Box_1.4_Right_RPI3.stl
3D Printed Parts/Ramps_Box_1.4_Top_RPI3.stl
3D Printed Parts/stepdown_converter_mount_a.stl
3D Printed Parts/stepdown_converter_mount_b.stl
CAD Files/Autodesk Inventor/8mm Acme Nut Block.ipt
CAD Files/Autodesk Inventor/8mm leadscrew 520mm.ipt
CAD Files/Autodesk Inventor/Aluminum Spacer 1.5in.ipt
CAD Files/Autodesk Inventor/Aluminum Spacer 3mm.ipt
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

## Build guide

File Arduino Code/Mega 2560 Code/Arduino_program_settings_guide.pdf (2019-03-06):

BARBOT Arduino setting Guide.

1. Install the Arduino IDE.
2. Install necessary libraries to the Arduino IDE

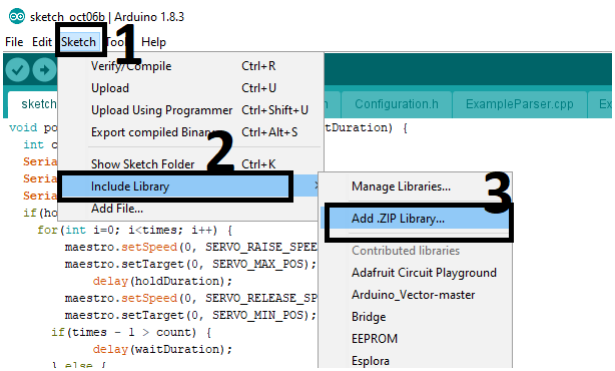
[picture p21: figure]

- Add “Arduino_Vector-master.zip”
- Add “Json_Streaming_Parser-1.0.5.zip”

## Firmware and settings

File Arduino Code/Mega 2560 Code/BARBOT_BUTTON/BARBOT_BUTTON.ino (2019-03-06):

#include "JsonInit_.h"

#include "AccelStepper.h"
#include "Configuration.h"
#include <Vector.h>
#include <Servo.h>

/*-------------------coin accepter time-------------*/
unsigned long coin_accepted_time_old = 0;
int coin_accepted = 0;



const int chipSelect = 53;

JsonInit_ mJson(chipSelect);

Vector<INGREDIENTS> v_i;
Vector<RECIPES> v_re;

AccelStepper stepper(X_INTERFACE_TYPE, X_STEP_PIN, X_DIR_PIN); // Define a stepper and the pins it will use
AccelStepper stepperZ(Z_INTERFACE_TYPE, Z_STEP_PIN, Z_DIR_PIN); // Define a stepper and the pins it will use



void serial_init(){
  Serial.begin(9600);
  while (!Serial) {
    ; // wait for serial port to connect. Needed for native USB port only
  }
  Serial.println("serial port inited");
}


void homeXAxis() {
    
  int endStopState = digitalRead(X_ENDSTOP_PIN); 
   while (endStopState == HIGH) {
    stepper.moveTo(100);
    stepper.setSpeed(X_HOME_SPEED);
    stepper.runSpeed();
   endStopState = digitalRead(X_ENDSTOP_PIN);  
  }  

  stepper.moveTo(stepper.currentPosition() - 50);
   while (stepper.distanceToGo() != 0) {
    stepper.setSpeed(X_PARK_SPEED * -1);
    stepper.runSpeed();      
  }
  
  endStopState = digitalRead(X_ENDSTOP_PIN);  
  while (endStopState == HIGH) {
     stepper.moveTo(100);
    stepper.setSpeed(X_PARK_SPEED);
    stepper.runSpeed();   
    endStopState = digitalRead(X_ENDSTOP_PIN);
  }

  stepper.setCurrentPosition(0); 
}


void moveXTo(int pos) {  
  
  Serial.print("X goes to: ");
  Serial.println(pos);
  
  if(pos <= 0 && pos >= X_MAX_POS) {
    stepper.setAcceleration(X_ACCELERATION);
    stepper.moveTo(pos);
      if(pos < stepper.currentPosition()) {
      
        stepper.setSpeed(-100);
      } else {
       
        stepper.setSpeed(100);
      }
    while(stepper.distanceToGo() != 0) {
      stepper.run(); 
    }
  } else {
    Serial.println("Position should be between -4995 and 0");
  }
}


void button_init(){    
  pinMode(16, INPUT_PULLUP); 
  pinMode(17, INPUT_PULLUP); 
  pinMode(23, INPUT_PULLUP); 
  pinMode(25, INPUT_PULLUP); 

  pinMode(27, INPUT_PULLUP); 
  pinMode(29, INPUT_PULLUP); 
  pinMode(31, INPUT_PULLUP); 
  pinMode(33, INPUT_PULLUP); 

  pinMode(35, INPUT_PULLUP); 
  pinMode(37, INPUT_PULLUP); 
  pinMode(39, INPUT_PULLUP); 
  pinMode(41, INPUT_PULLUP); 

  pinMode(43, INPUT_PULLUP); 
  pinMode(45, INPUT_PULLUP); 
  pinMode(47, INPUT_PULLUP);  
  pinMode(32, INPUT_PULLUP);  
  
  pinMode(18, INPUT_PULLUP); // Coin Accepter signal input
  pinMode(19, INPUT_PULLUP); // Debugging button
  
}
  
void setup() {
  
  // Open serial communications and wait for port to open:
  pinMode(24, OUTPUT);   // enable A4988
  digitalWrite(24, LOW); // enable A4988

  pinMode(30, OUTPUT);   // enable A4988
  digitalWrite(30, LOW); // enable A4988

  
  serial_init();
  button_init();
  
  
  mJson.Init_("INGRED~1.JSO","RECIPE~1.JSO");
  Serial.println("Json Testing-----------------------");

      
  v_re = mJson.listener_RECIPE.vi_recipe_item;
  v_i  = mJson.listener_INGRED.vi;

  Serial.println(v_re.size());
//  mJson.Init_("ingredients.json","recipes.json");
  stepper.setMaxSpeed(X_MAX_SPEED); // Sets the maximum speed the X axis accelerate up to
  stepperZ.setMaxSpeed(Z_MAX_SPEED); // Sets the maximum speed the Z axis accelerate up to
  pinMode(Z_ENDSTOP_PIN, INPUT_PULLUP); // Initialize Z- endstop pin with the internal pull-up resistor enabled 
  pinMode(X_ENDSTOP_PIN, INPUT_PULLUP); // Initialize X- endstop pin with the internal pull-up resistor enabled
  pinMode(14, INPUT_PULLUP);// for Stop Interrupt
  pinMode(15, INPUT_PULLUP);// for Home z, x 
  homeZAxis(); // Return the Z axis to it's home position at the startup
  homeXAxis(); // Return the X axis to it's home position at the startup


  coin_accepted = 0;
}
void coin_acceptor_handler(){
  if (digitalRead(18) == 0){ // coin accepted 
    delay(100); // --------------------------------------- coin accepting delay time
    coin_accepted = 1;
    coin_accepted_time_old = millis();
  }
}
void loop() {
 
  unsigned long current_time = 0;  
  coin_acceptor_handler();  
  button_scheduler();
  current_time = millis();
  if ((current_time - coin_accepted_time_old) > 60000) // no reponse for 60s
  {
    coin_accepted_time_old = current_time;
    coin_accepted = 0;
  }
  delay(5);
}


int get_button_state(){      
  if (!digitalRead(16)) return 0;
  if (!digitalRead(17)) return 1;
  if (!digitalRead(23)) return 2;
  if (!digitalRead(25)) return 3;
  
  if (!digitalRead(27)) return 4;
  if (!digitalRead(29)) return 5;
  if (!digitalRead(31)) return 6;
  if (!digitalRead(33)) return 7;
  
  if (!digitalRead(35)) return 8;
  if (!digitalRead(37)) return 9;
  if (!digitalRead(39)) return 10;
  if (!digitalRead(41)) return 11;  

  if (!digitalRead(43)) return 12;  
  if (!digitalRead(45)) return 13;  
  if (!digitalRead(47)) return 14;    
  if (!digitalRead(32)) return 15;    
  
  return 100;
}

void get_RecipeData(int butState){
  int bufIndex = butState;
  for (int i = 0; i < v_re.size(); i++){
    if(v_re[i].id == 0 && v_re[i].amount == 0) {bufIndex--; continue;}
    if (bufIndex < 0) return;
    if (bufIndex == 0){
      moveXTo(v_i[v_re[i].id - 1].coordinate);  
      pourZ(v_re[i].amount/ 20,v_i[v_re[i].id - 1].hold, v_i[v_re[i].id - 1].wait);      
    }
  }
}

void button_scheduler(){   
 if (digitalRead(19) &&!coin_accepted) return;  
 int butState = get_button_state();
 if (butState == 100) return; 
 coin_accepted = 0; 
 get_RecipeData(butState); 
 moveZTo(0); // Return the Z axis to it's home position at the startup
 Serial.println("return to x home");
 moveXTo(0); // Return the X axis to it's home position at the startup

}

void homeZAxis() {          
  
        int endStopState = digitalRead(Z_ENDSTOP_PIN);         
        while (endStopState == HIGH) {
        
          stepperZ.moveTo(50);
          stepperZ.setSpeed(Z_HOME_SPEED);
          stepperZ.runSpeed();
          endStopState = digitalRead(Z_ENDSTOP_PIN);  
        }  
        
        stepperZ.moveTo(stepperZ.currentPosition() - 25);
        
        while (stepperZ.distanceToGo() != 0) {        
          stepperZ.setSpeed(Z_PARK_SPEED * -1);
          stepperZ.runSpeed();            
        }
        endStopState = digitalRead(Z_ENDSTOP_PIN);

      
        while (endStopState == HIGH) {
          stepperZ.moveTo(50);        
          stepperZ.setSpeed(Z_PARK_SPEED);
          stepperZ.runSpeed();   
          endStopState = digitalRead(Z_ENDSTOP_PIN);
        }  
       
        stepperZ.setCurrentPosition(0); 
      }
      
void moveZTo(int pos) {    
            
      Serial.print("Z goes to: ");
      Serial.println(pos);    
      
      stepperZ.setAcceleration(Z_ACCELERATION);
      stepperZ.moveTo(pos);
      
      if(pos < stepperZ.currentPosition()) {
            stepperZ.setSpeed(-100);
          } else {
            stepperZ.setSpeed(100);
          }
        while(stepperZ.distanceToGo() != 0) {
          stepperZ.run(); 
        }      
    }
 
void pourZ(int times, int holdDuration,int waitDuration) {
        int count = 0; // Pour counter 
        if(holdDuration > 0 && waitDuration > 0) {
          for(int i=0; i<times; i++) {            
              moveZTo(Z_MAX_POS);
              delay(holdDuration - HOLD_DELAY_IN_Z_MAX);              
              moveZTo(0); // Return the Z axis to it's home position at the startup
             if(times - 1 > count) {
                      delay(waitDuration);
                } else {
                      delay(DELAY_BETWEEN_INGREDIENTS);
                }
              count++;
            }
        } else {
          Serial.println("Hold and wait duration parameters cannot be lower than or equal to 0");
        }
}

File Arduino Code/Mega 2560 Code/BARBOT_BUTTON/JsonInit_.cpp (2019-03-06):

#include "JsonStreamingParser.h"
#include "JsonListener.h"
#include "ExampleParser.h"
#include <SPI.h>
#include <SD.h>
#include "JsonInit_.h"
//#define IS_DEBUGGING_WITHOUT_SD


#ifdef IS_DEBUGGING_WITHOUT_SD
void JsonInit_::JSON_withoutsd_init(){ 
  Serial.println("JSON_withoutsd_init");
  listener_INGRED.init_listen(1);
  parser_INGRED.setListener(&listener_INGRED);
     
  listener_RECIPE.init_listen(2);
  parser_RECIPE.setListener(&listener_RECIPE);
  
  listener_INGRED.INGREDinitWithoutSD();
  listener_RECIPE.INGREDinitWithoutSD();
  
  return true;
}

#endif
boolean SDCARD_Init(int cs){
   Serial.print("Initializing SD card...");
   // see if the card is present and can be initialized:
   
   if (!SD.begin(cs))  {
       Serial.println("Card failed, or not present");
       // don't do anything more:  
       return false;
  }
    Serial.println("card initialized.");
    return true;
}


boolean JsonInit_::JSON_INGRED_init(String INGRED_name){  
  char jsonBuf[128];  
  // open the file. note that only one file can be open at a time,
  // so you have to close this one before opening another.
  File dataFile = SD.open(INGRED_name);
  //File dataFile = SD.open("ingredients.json");
  // if the file is available, write to it:
  
  listener_INGRED.init_listen(1);
  parser_INGRED.setListener(&listener_INGRED);
   
  if (dataFile) {
    while (dataFile.available()) 
    {
       dataFile.read(jsonBuf,128);              
       for (int i = 0; i < sizeof(jsonBuf); i++) 
       {        
          parser_INGRED.parse(jsonBuf[i]); 
       }
     
    }       
    dataFile.close();
    Serial.println("JSON init Secceed");       
  }
  // if the file isn't open, pop up an error:
  else 
  {
    Serial.println("JSON init failed");    
    return false;
  }
  return true;
  
}



boolean JsonInit_:: JSON_RECIPE_init(String RECIPE_name){
  
  char jsonBuf[128];  
  // open the file. note that only one file can be open at a time,
  // so you have to close this one before opening another.
  File dataFile = SD.open(RECIPE_name);
  //File dataFile = SD.open("ingredients.json");
  // if the file is available, write to it:
  listener_RECIPE.init_listen(2);
  parser_RECIPE.setListener(&listener_RECIPE);
   
  if (dataFile) {
    while (dataFile.available()) 
    {
       dataFile.read(jsonBuf,128);          
       for (int i = 0; i < sizeof(jsonBuf); i++) 
       {        
          parser_RECIPE.parse(jsonBuf[i]); 
       }
      
    }       
    dataFile.close();
    Serial.println("JSON init Secceed");       
  }
  // if the file isn't open, pop up an error:
  else 
  {
    Serial.println("JSON init failed");    
   return false;
  }
  return true;
}
JsonInit_::JsonInit_(int mchipSelect){
	
   chipSelect = mchipSelect;
}

boolean JsonInit_::Init_(String INGRED_name, String RECIPE_name) { 
#ifndef IS_DEBUGGING_WITHOUT_SD
  if(!SDCARD_Init(chipSelect))return false;
  if(!JSON_INGRED_init(INGRED_name))return false;
  if(!JSON_RECIPE_init(RECIPE_name))return false;
#else
  Serial.println("JSonInit__");
  JSON_withoutsd_init();
#endif
  return true; 
}

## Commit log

2019-03-06 Add files via upload
    Electronic Housing (mega2560,raspberry 2560, Levelshifter, Stepdownconverter)
    [Display_01.stl, Display_cover_2.stl, Level-Shifter.stl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]
2019-03-06 folder reorganized
    [200mm x 165mm- Bottom v1.dxf, 200mm x 165mm- Top v1.dxf, 233mm x 200mm- Upper Front v1.dxf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]
2019-03-19 new parts
    new parts
    [Belt-tensioner.stl, cbb.stl, cbb1.stl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]
2019-12-05 Create Laser Cut Panels.zip
